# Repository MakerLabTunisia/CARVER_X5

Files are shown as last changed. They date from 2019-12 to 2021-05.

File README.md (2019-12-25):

# CARVER  X5, the Open source 5 Axis CNC Machine

# Story:

## MakerLab :

MakerLab is a Tunisian tech startup specialized in developing customized embedded systems and mechatronics projects to industrials.  
In MakerLab, we believe in the Open Source Hardware philosophy and we want to spread the tech knowledge we gain, with the community so everyone performs itself and benefits from others experiences.        And this is why, we made from our little space in Sousse, a **TechSpace**, open for everyone who wants to work on real projects, finding all what a Maker needs to create his own tech project.  
In our TechSpace, many projects were developed and created, even if it is by our staff or by students from different universities across the country, starting from Drones, Internet of Things (IoT) devices, arriving to Robotic Arms and CNC Machines.  
Moreover, this 5 Axis CNC Machine, is our first Open Source Hardware Project we made, and which we are so happy sharing it with the community. 
You can find more details on our TechSpace in our:  
Lien Facebook : https://www.facebook.com/tunmakerlab/
Lien siteweb : https://makerlab.tn/

## Presenting the project:

This 5 axis CNC machine, is part of a big project made by our partners Open Lab Hamburg from the Helmut Schmidt University in Germany, for the benefit and with the collaboration of FABLAB ENIT (National School of Engineering of Tunis), and sponsored by the BMBF. 

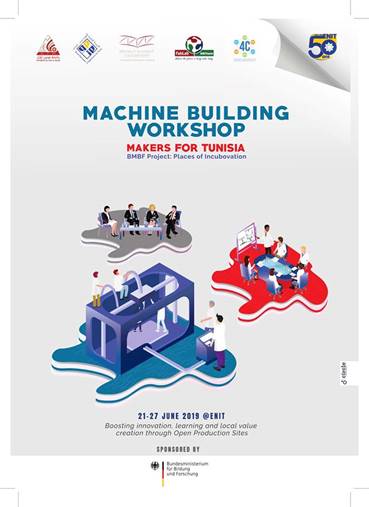
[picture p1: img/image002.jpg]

<div align="center"><i>Machine Building Workshop</i></div>
This project consists of organizing a one-week workshop for building machines, and we, MakerLab’s staff, are happy and glad to be part of this first of its kind project in our beloved country, Tunisia.

# Why a 5 axis CNC Machine?

Being always updated to the latest OSHW projects in the community, we found that there is many 3 Axis CNC machines, 3D Printers and Laser Cutter with a very good documentation, but not enough OSHW 5 Axis CNC machines and not at all for the Head/Head type. 

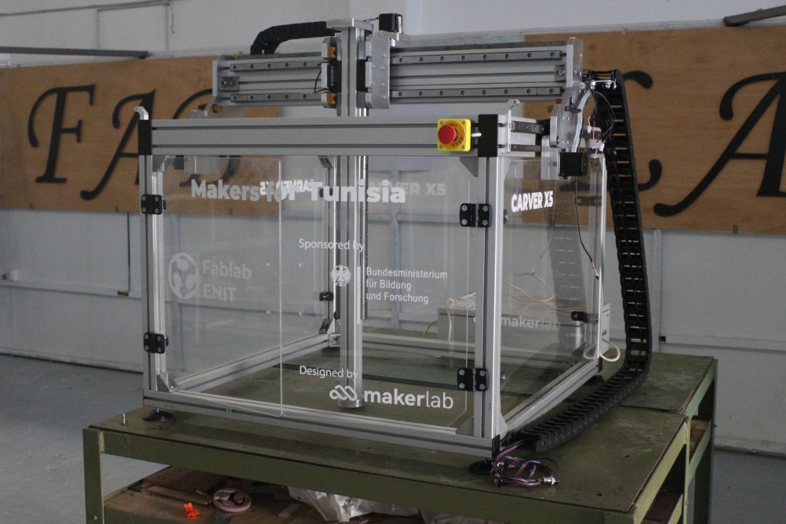
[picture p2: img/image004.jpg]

<div align="center"><i>CARVER X5 Machine</i></div>
So we thought we could create the first OSHW, Head/Head, double swivel head form, 5 Axis CNC Machine. We tried our best to make it both robust and easily replicable machine. Constructed mainly from Heavy Aluminum Extrusion profiles, and thick aluminum milled parts, HGR25 Linear guides, using NEMA23 Stepper motors, and Rack and pinion for transmission, Carver X5 is capable of milling materials like wood, plastics and composite materials.

# CARVER X5 Machine

## 1. Specifications

**Dimensions 5xm600** 	      : 650 x 670 x 480mm  
**Working volume 5xm600**   : 990 x 780 x 1000mm  
**Max travel speed XYZ**	      : 15000mm/min (X,Y);     3000-6000mm/min (Z)  
**Max travel speed BC**            : 20rpm(C)  20rpm(B)  
**Motors used**                           : NEMA 23 ( X / Y / Z / B / C)  
**Linear guides**                         : HIWIN High accuracy Rails and Blocks  
**Structure material**               : Anodized Aluminum   
**Protection**                              : 5mm Acrylic enclosure  
**Power requirements**           : 1200W, 220V, 60hz, 13A   
**Weight**        	           		      : 85kg  
**Computer interface**             : USB  
**Computer requirements**    : Windows operating system with Mach3  
**Controller**                               : MACH3 (to be purchased separately from an official vendor)  
**Software**                                 :  supports any CAD/CAM software   

## 2. Machine design

CNC machines are commonly known that they are nothing more than automated robots, their famous type, is a 3 axis CNC machines, which are considered as 3P robots (robot with 3 Prismatic Joints linked with 4 Links).  

But in 5 axis CNC machines we talk about 3P2R robots, because they are composed of 3 Prismatic Joints succeeded with 2 Revolute Joints, and linked with 6 Links.

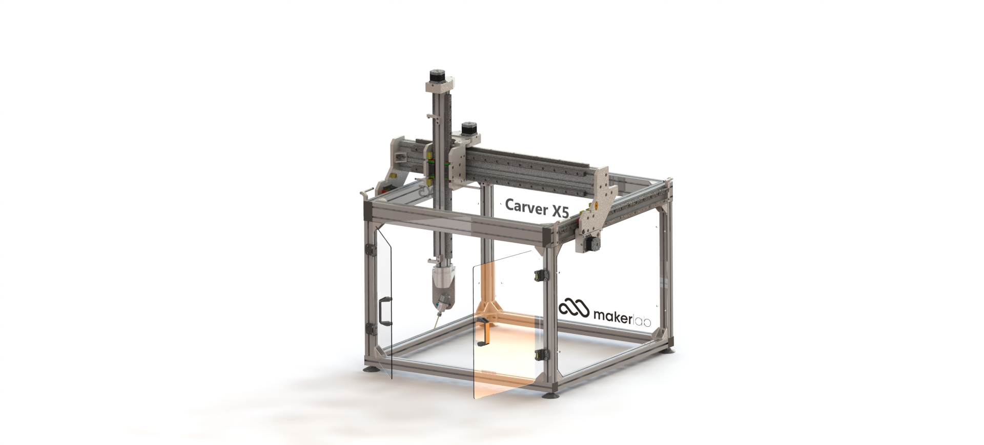
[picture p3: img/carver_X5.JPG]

<div align="center"><i>CARVER X5 Design</i></div>
Our Joints are named (X, Y, Z, C & B)

The Links are named : Frame, Y2X Bridge, X2Z, Z Axis, Swivel Head and the Spindle.

## 3. Machine composition:

### ▪ Frame 

Designed to be easily made, assembled and disassembled, we choose the aluminum profile to be the main structure composition.
As it's important that the structure be stiff and robust, we wanted to work with 45 series aluminum profiles.

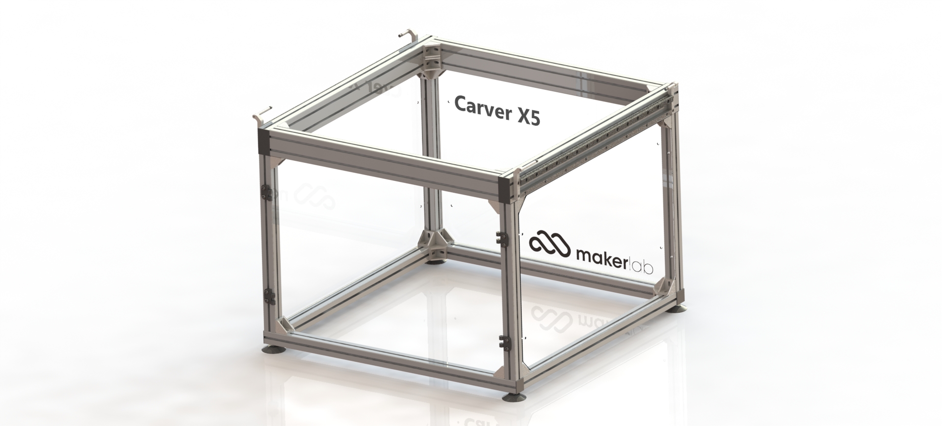
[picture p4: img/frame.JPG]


<div align="center"><i>Machine Frame</i></div>
The machine frame contains the rails and transmission rack of the Y-axis that will carry the other entire axis, this is why we worked with the 45x90 aluminum profiles in the top stage.
The frame carries the mechanical stops; they include a screw to adjust the limit position.

### ▪ Y2X Bridge

The Y2X Bridge is the second link in our 5-axis CNC machine, it links the Y and X joints.

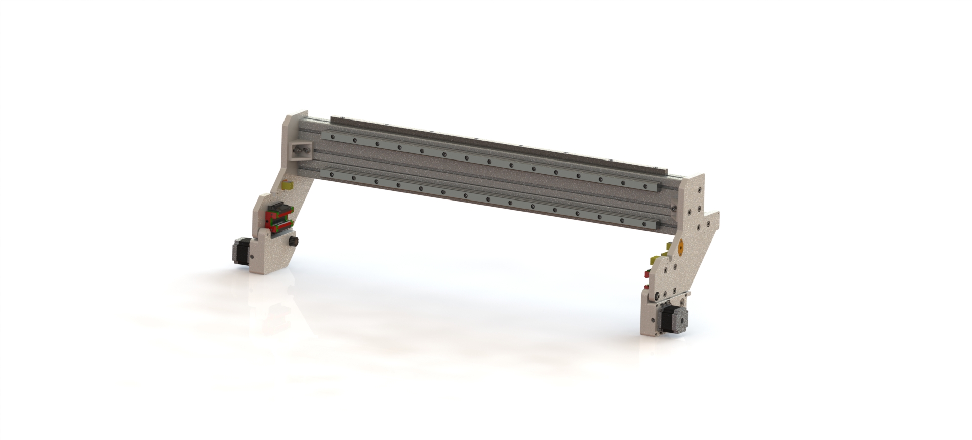
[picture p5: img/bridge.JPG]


<div align="center"><i>Y2X Bridge</i></div>
Constructed from two perpendicular 45x90 aluminum profile and two 15mm aluminum plate flanks on which will be installed the Y-axis sliding blocks.

### ▪ X2Z 

X2Z, as its name indicates, do the function of the joint between the two prismatic axis, X and Z.
X2Z is an assembly that plays a big role in our 5 Axis CNC Machine, because it assures both, the linear guiding of X axis, Z axis and their transmission organs.

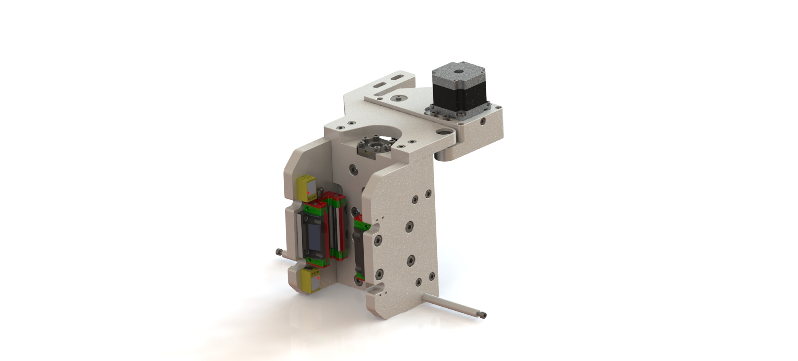
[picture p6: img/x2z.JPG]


<div align="center"><i>X2Z</i></div>
Built totally from thick aluminum plates, X2Z contains the sliding blocks of X-axis installed on its back, and those of the Z-axis, installed between the two X2Z flank plates.
On the X2Z assembly, get installed the X Motor Module and the Z-axis ball bearing Nut.

###  ▪ Z Axis

The Z-axis, slides on the 2 blocks installed on the X2Z Flank plates. The motor module installed on its top assures its motion. The Z motor transmit rotation to the ball screw that moves the Z-axis up and down.

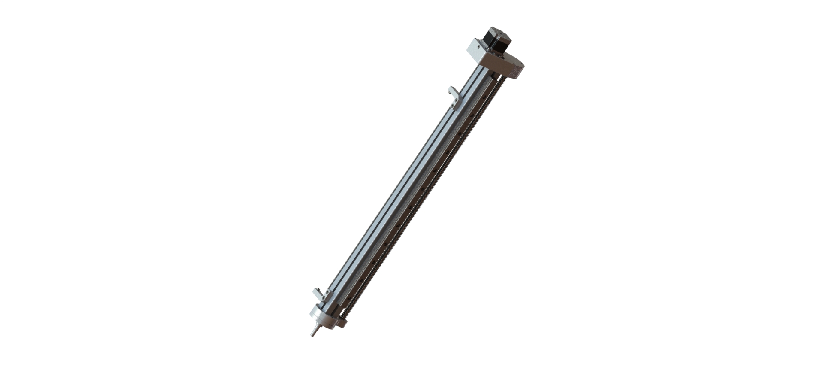
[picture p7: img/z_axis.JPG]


<div align="center"><i>Z Axis</i></div>
In its bottom is installed the swivel head that rotates the end effector around 2 axis.

###  ▪ Swivel Head

The swivel head is composed from the last two revolute joints, C & B.
What is special about this assembly, is the fact that it should be the more compact possible. So the two motors, their transmission system and even the limit switches and connectors should all be enclosed in this assembly, and this was the hardest task that we encountered in the whole machine design.
While designing the Swivel Head, there was 2 big challenges, the choice of transmission system and minimizing joints offset relatively to each other.

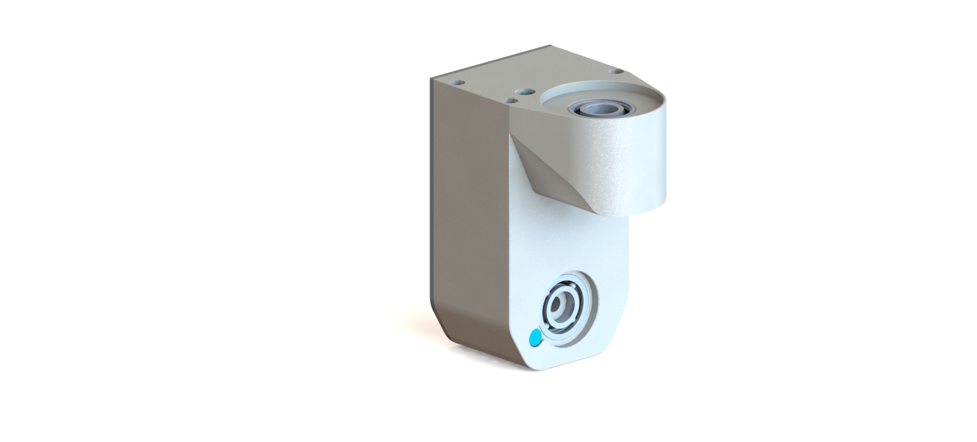
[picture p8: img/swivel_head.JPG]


<div align="center"><i>Swivel Head</i></div>
There is challenge because C and B axis will handle big effort while milling, and if mounted directly on the motor shaft or even through a reversible transmission system, this may cause a loss in steps when encountering big efforts. This obliged as to work with worm gear, which is an irreversible transmission system.

### ▪ Spindle Motor

For the spindle motor, we did our best to find small and powerful, and not too expensive ones in the market, but we found none.
The main specification needed is a small size, but the most of powerful spindles are so big that you cannot integrate in the swivel head.
This is why we designed and fabricated our own spindle composed of a 540W Brushless motor, a bearing housing and an ER11 chuck.

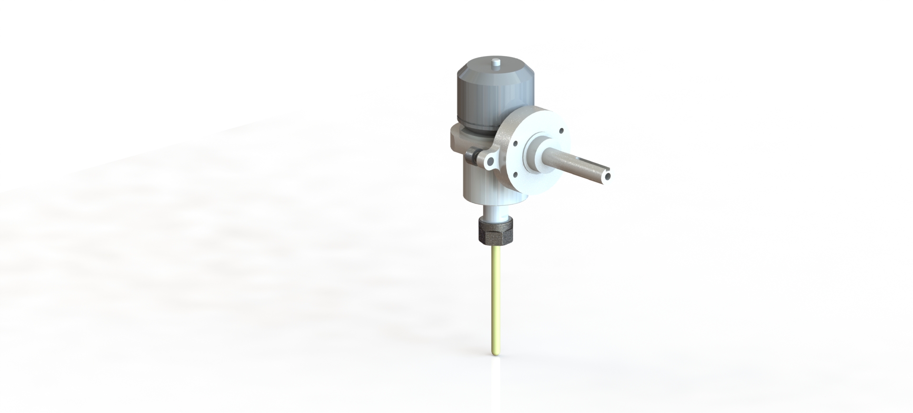
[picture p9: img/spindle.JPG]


<div align="center"><i>Spindle Motor</i></div>
The spindle motor is capable of a max velocity of 20000 RPM at 24V, and has enough torque for milling wood and plastics.

### ▪ Motor Modules

Machine movement along X, Y and Z Axis is assured by 4 motor modules.  Containing pulley and belt transmission system between the motor shaft and the shaft.

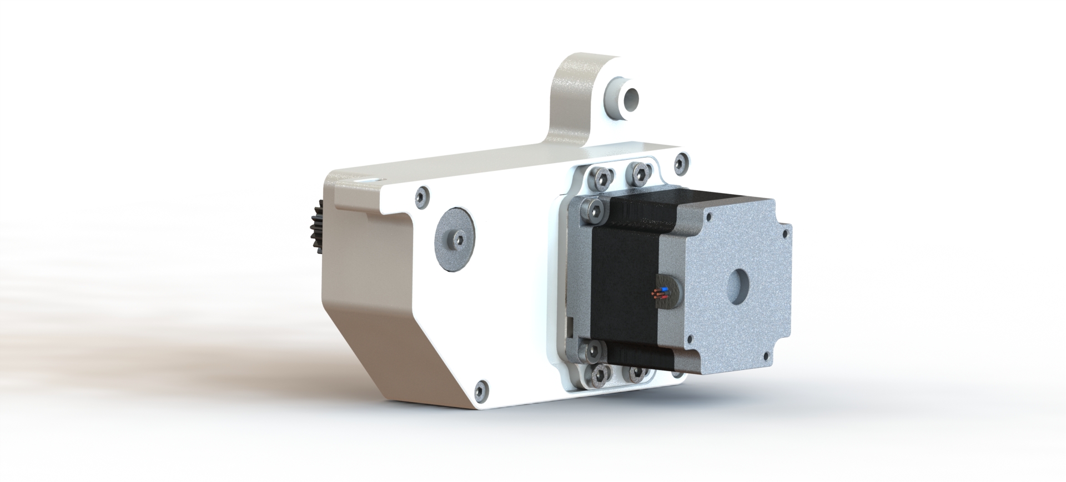
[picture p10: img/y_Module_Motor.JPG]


<div align="center"><i>X/Y Axis Motor Module</i></div>
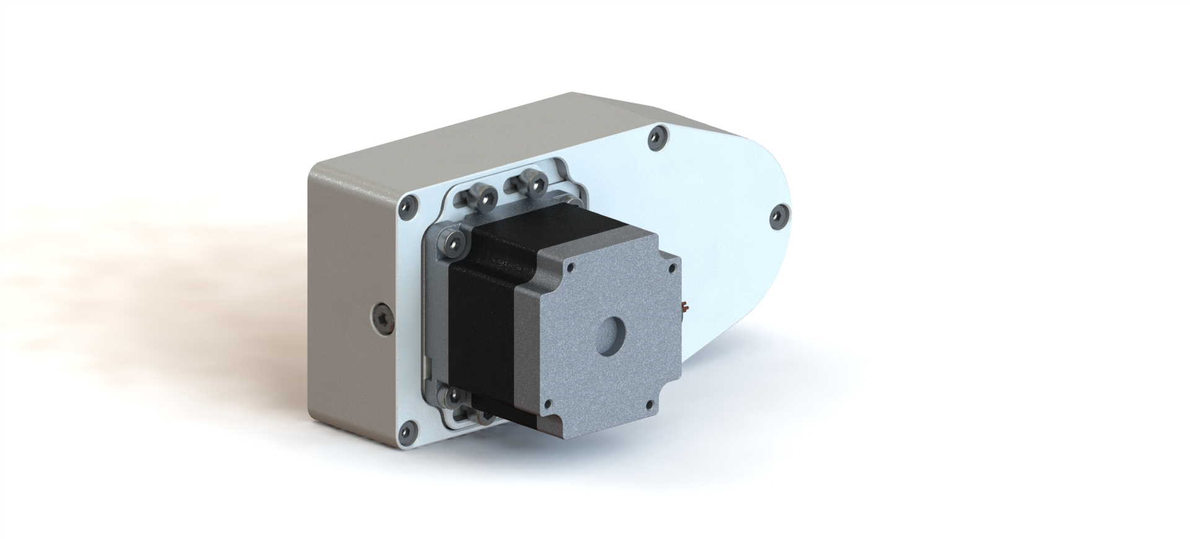
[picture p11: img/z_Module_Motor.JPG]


<div align="center"><i>Z Axis Motor Module</i></div>
## 4. Electronic enclosure

Installed in an industrial **[plastic enclosure](http://www.akisplastik.com.tr/en-us/Product/ProductCategoriesDetail?categoryId=12)** (400x500x240), the **electronics** of the **CARVER X5** is composed of a set of drivers for each motor including the spindle driver, a USB interface control board, a sensor interface board and two 12v 42A DC Power Supply. 

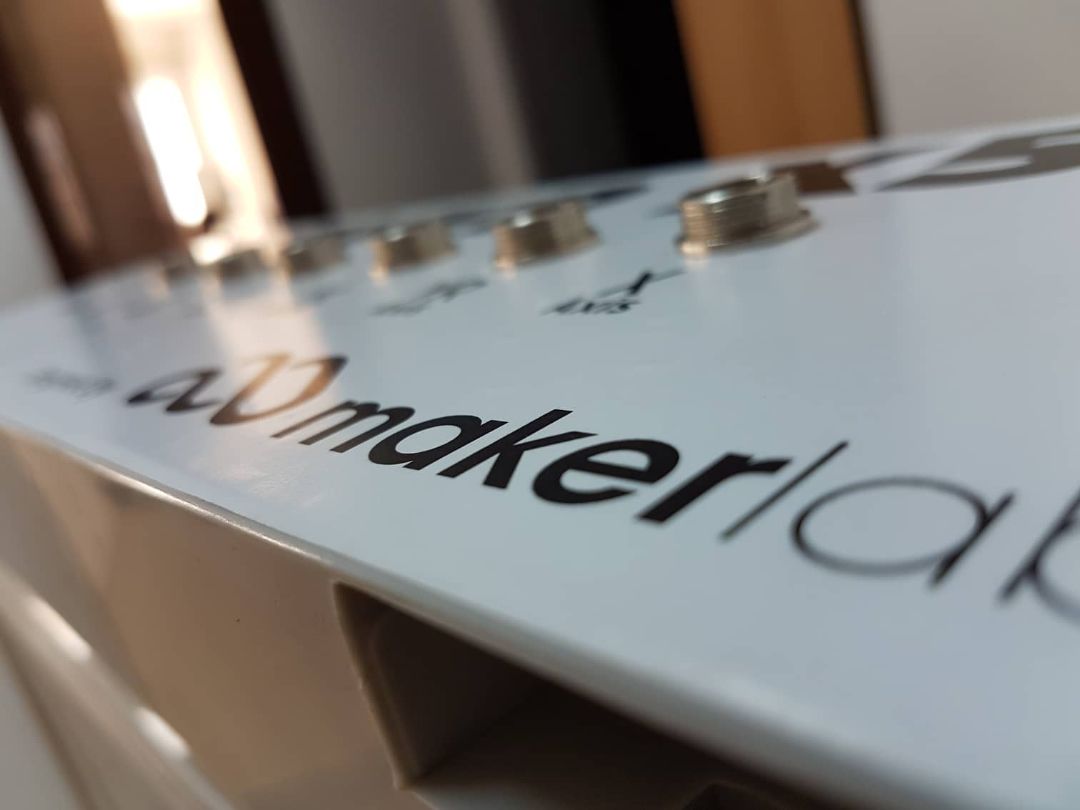
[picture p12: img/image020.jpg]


▪ **THE PoKeys57CNC control board**
PoKeys57CNC USB and Ethernet CNC controller is a blend between general purpose PoKeys device and motor controller. The device is targeted primarily for controlling up to 8 STEP/DIR signal driven motors (stepper motors, servo drives, etc.) in various applications with the addition of powerful PoKeys device features. 

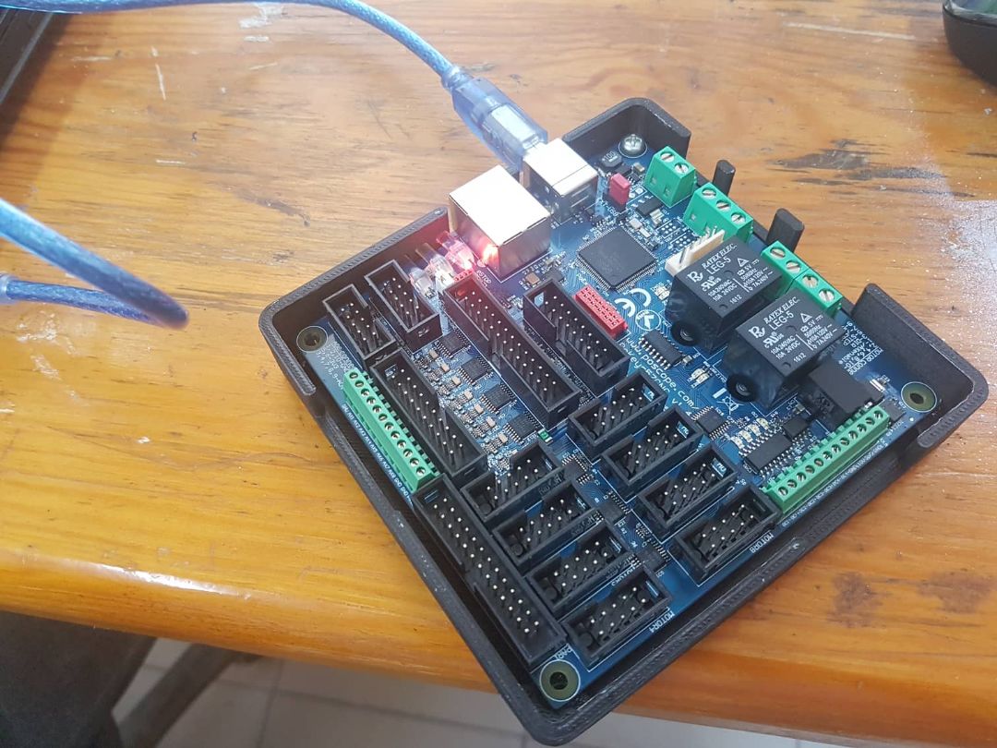
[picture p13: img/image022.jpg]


 Download PoKeys57CNC datasheet [here](https://www.poscope.com/wp-content/uploads/downloads/Pokeys/Manuals/PoKeys57CNC%20user%20manual.pdf).

▪ **Drivers**
TB6600 Stepper Motor Driver is an easy-to-use stepper motor driver, which could control a two-phase stepping motor. It is compatible with Arduino and other microcontrollers that can output a 5V digital pulse signal. TB6600 stepper motor driver has a wide range power input, 9~42VDC power supply. And it is able to output 4A peak current, which is enough for the most of stepper motors. The stepper driver supports speed and direction control. You can set its micro step and output current with 6 DIP switch.

Download TB6600 datasheet [here](http://olimex.cl/website_MCI/static/documents/TB6600_data_sheet.pdf).

▪ **The sensor cables gatherer board**
The need for the sensor cable gatherer board has emerged due to the multiplicity of sensors. And to minimize the number of cables passing through the cables carrier, first, we managed to gather them in a 15 cores VGA cable, then we choose to use 2 DB9 ports and cables, one for Limites (+), and the other for Limites (-).  

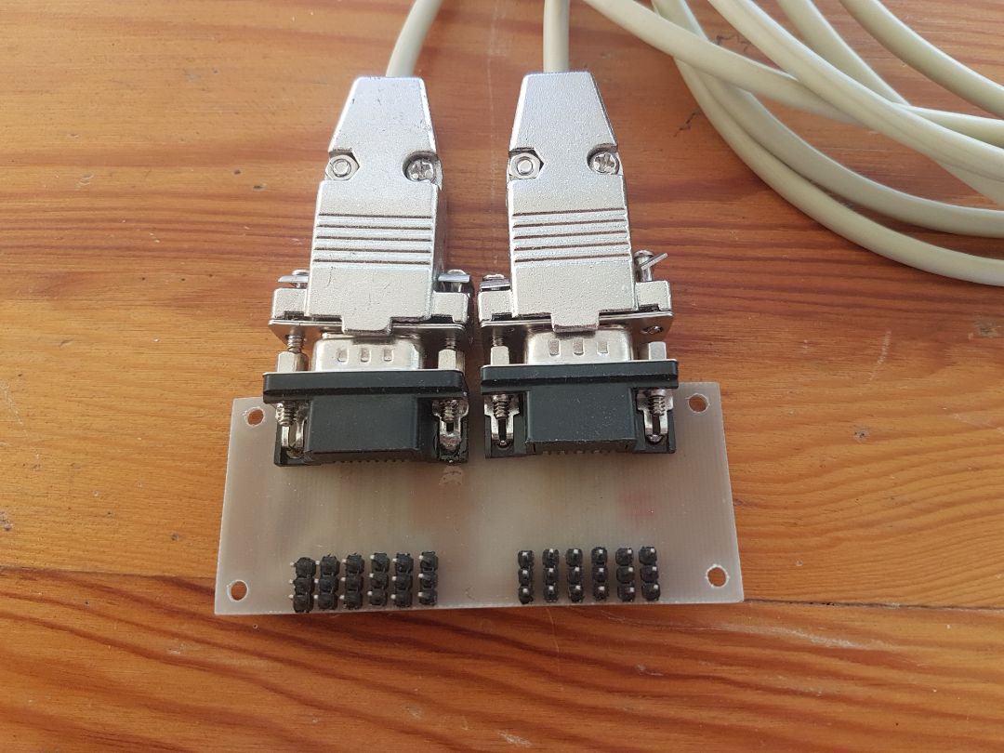
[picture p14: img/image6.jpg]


This board provides the current and voltage needed to all the 10 sensors used in the machine and the toggle switch, and is installed on the Y2X Bridge in between the two cables carrier.   

(Board KiCAD)

▪ **The sensors interface board**
This board will play the role of the interface between sensors signals coming from the first board and the pokeys57cnc board through a little circuit of signal adaptation.  
Inductive proximity switches works with 12V power supply, and returns a 12V digital signal, but the pokeys57cnc can only handle 5V digital signal in limit switches inputs. 

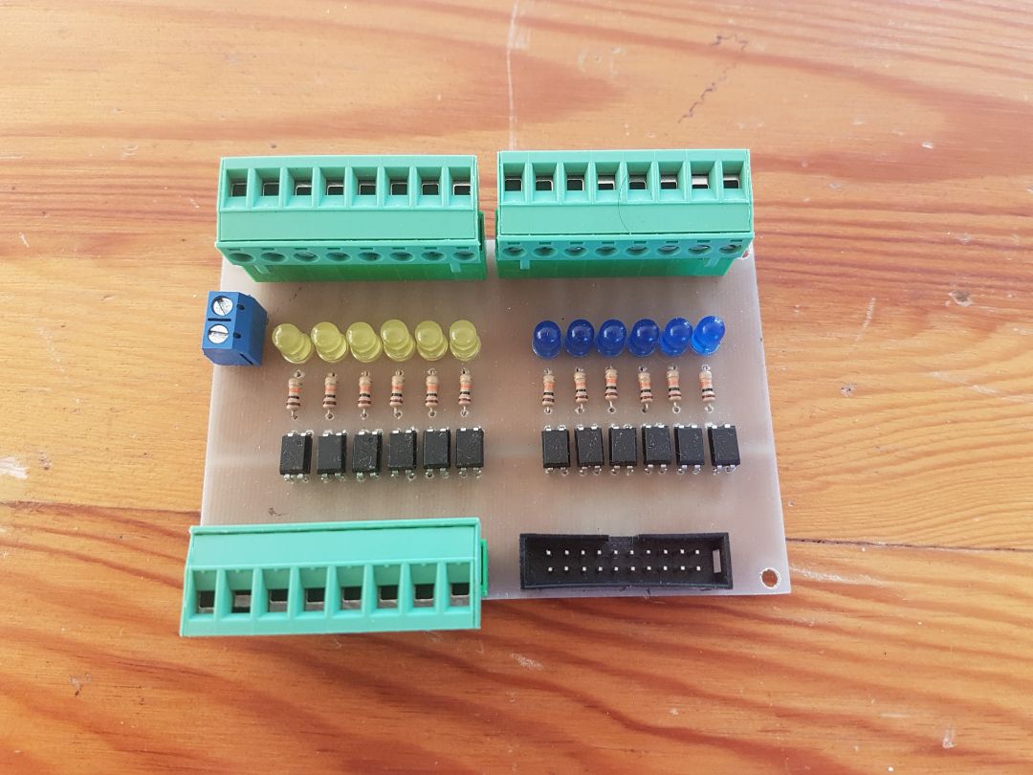
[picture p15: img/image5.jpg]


This is why we used a circuit based on a 470 ohm resistor for current limiting and a 5.1V zener diode to let only the needed 5V pass to the control board for each signal. 

▪ **Spindle motor Driver**
As we created our own spindle based on brushless DC Motor, we used its recommended Electronic Speed Controller as a driver. A 60A ESC is responsible of driving the motor at 20 000 RPM at 24V.
Product page [Link](https://www.overlander.co.uk/overlander-xp2-60a-sbec-brushless-esc-rtf-speed-controller.html).

## 5. Wiring

 One main task we did is the wiring, and it is so important.
 We used RGB 4 wire Cables for the stepper motors, they are thick enough to carry the needed current.
 The end stop switches cables were long enough to reach the first interface board installed on the bridge assembly.
 We gathered all sensors signals in two RS232 cables to facilitate connection.
 Of course all these cables needed a way to be placed in, so we used 57x25 industrial cable carrier to arrange all wires to the electronic enclosure.

## 6. Software

### ▪ Fusion360 : CAM software
Fusion 360 combines industrial and mechanical design, simulation, collaboration, and machining in an integrated concept-to-production toolset.
Fusion 360 is the first 3D CAD, CAM, and CAE tool of its kind. It connects your entire product development process in a single cloud-based platform that work both on PC and MAC.

Download [Link](https://www.autodesk.com/products/fusion-360/students-teachers-educators).

### ▪ Pokeys Software : Software for the CNC Interface Board
PoKeys software setup package contains PoKeys configuration tool (also used for firmware updating), USB drivers, manuals, PoBlocks tool, Mach3 plugin etc. After installation, run the PoKeys application to update the firmware of PoKeys devices.

Configuration explanation video [Link](https://www.youtube.com/watch?v=qxPZVYqWExU).

Download [Link](https://www.poscope.com/downloads/).

### ▪ Mach3 : CNC Machine Controller Software

Mach3 turns a typical computer into a CNC machine controller. It is very rich in features and provides a great value to those needing a CNC control package.

Configuration explanation video [Link](https://www.youtube.com/watch?v=e5MjEEe-gE4&t=58s).

Download [Link](https://www.machsupport.com/downloads-updates/).

# Machine Building Workshop

The Machine Building Workshop was a great experience to all of us, and it was the first step to sharing knowledge with everybody.

This is a set of photos describing the general atmosphere in which passed this wonderful workshop.

## **▪ Day 1** 
**Ice breaking & debriefing around CNC machines and their purposes**
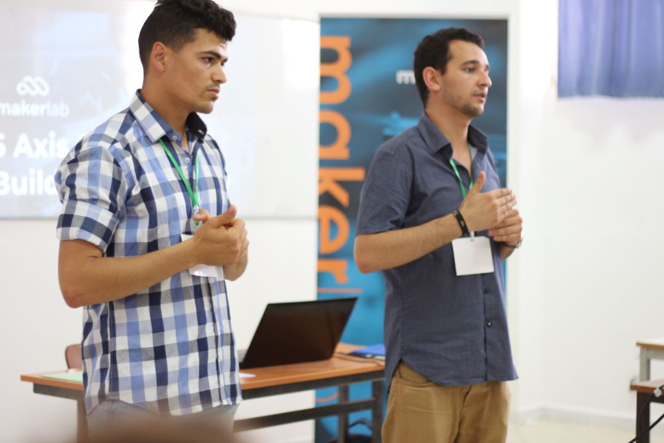
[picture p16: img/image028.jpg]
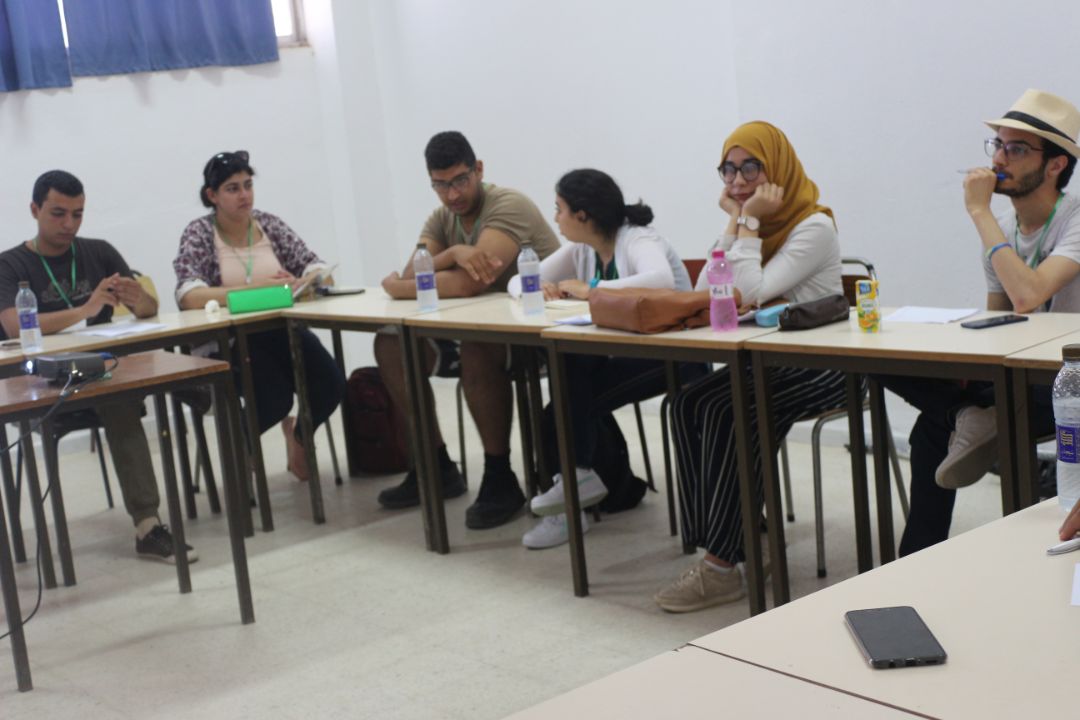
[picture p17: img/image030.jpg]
 

## ▪ Day 2 
Knowing everything about the design of the **CARVER X5** and the different steps will do during the workshop

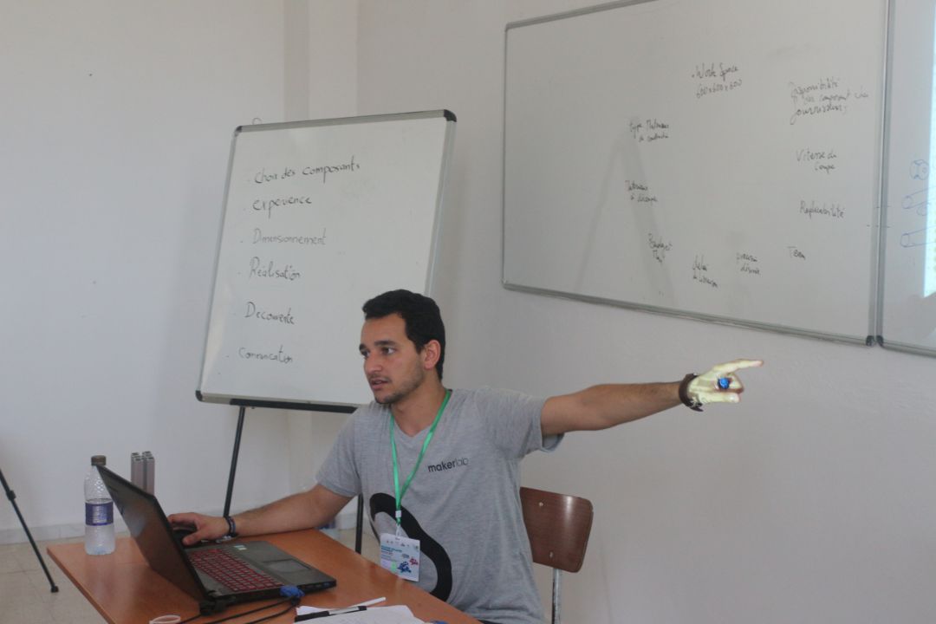
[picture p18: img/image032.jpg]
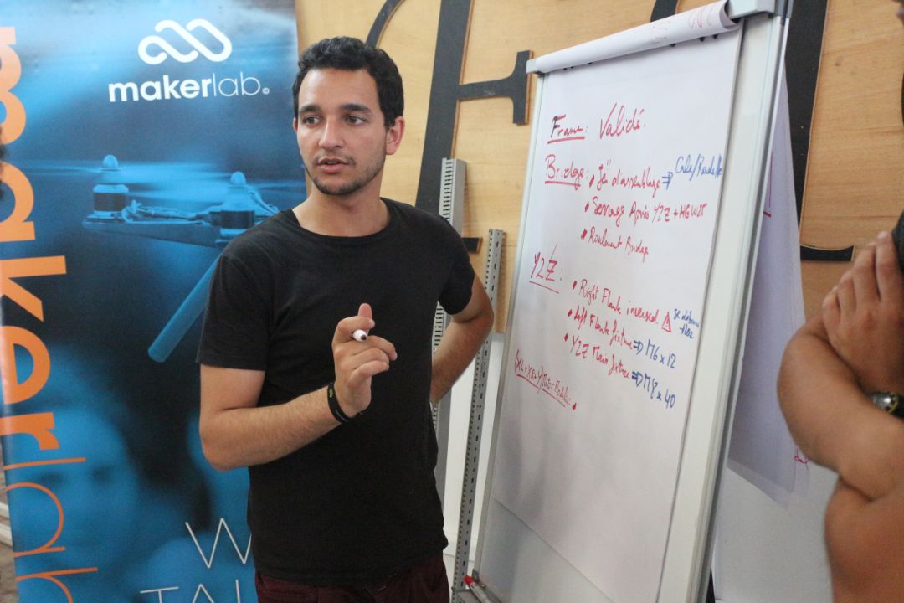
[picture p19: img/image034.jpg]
 

## ▪ Day 3 

**-Workbench and space preparation** 

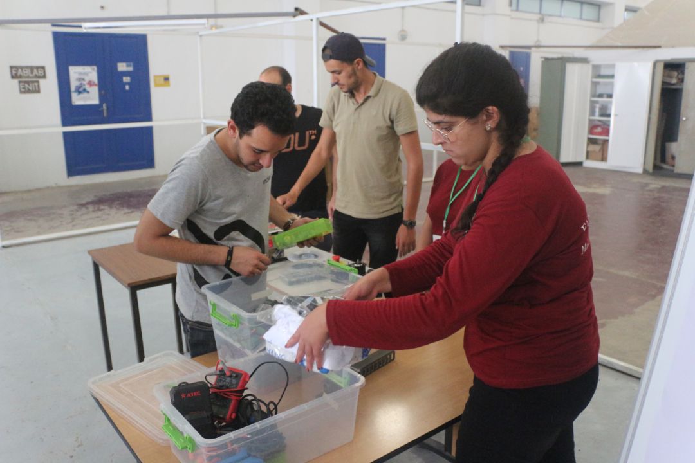
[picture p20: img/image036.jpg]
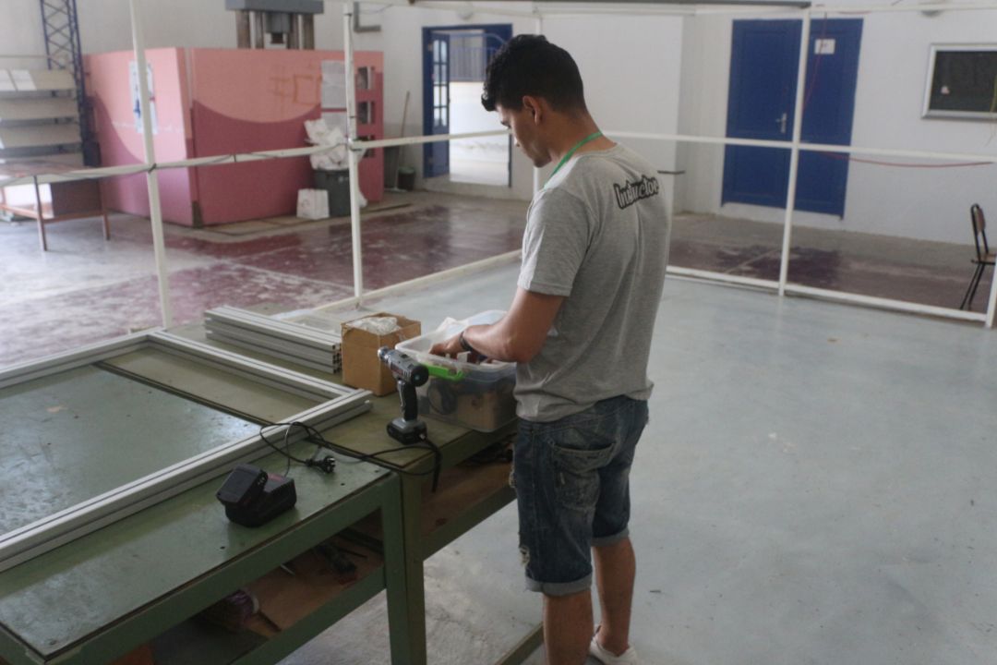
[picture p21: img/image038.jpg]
 

**-Frame assembly**

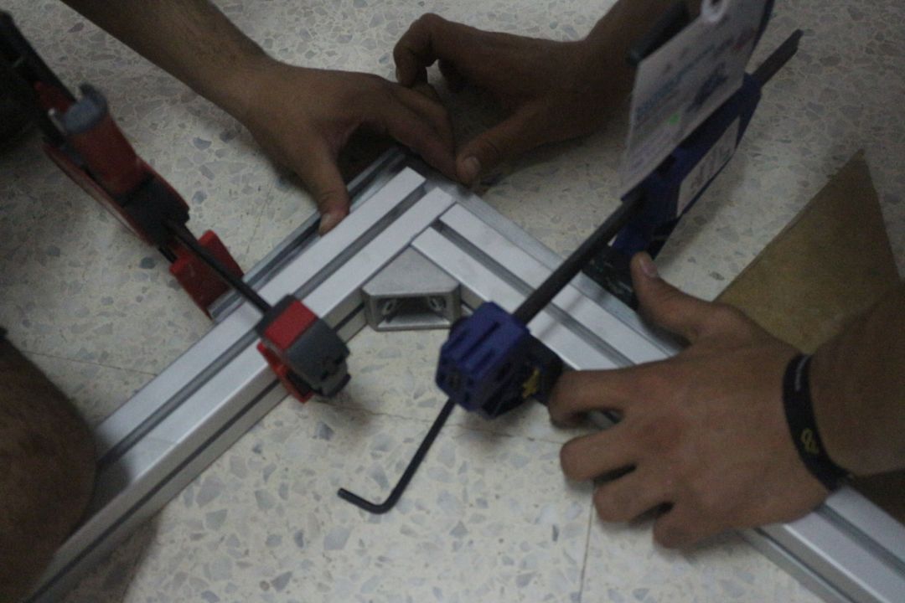
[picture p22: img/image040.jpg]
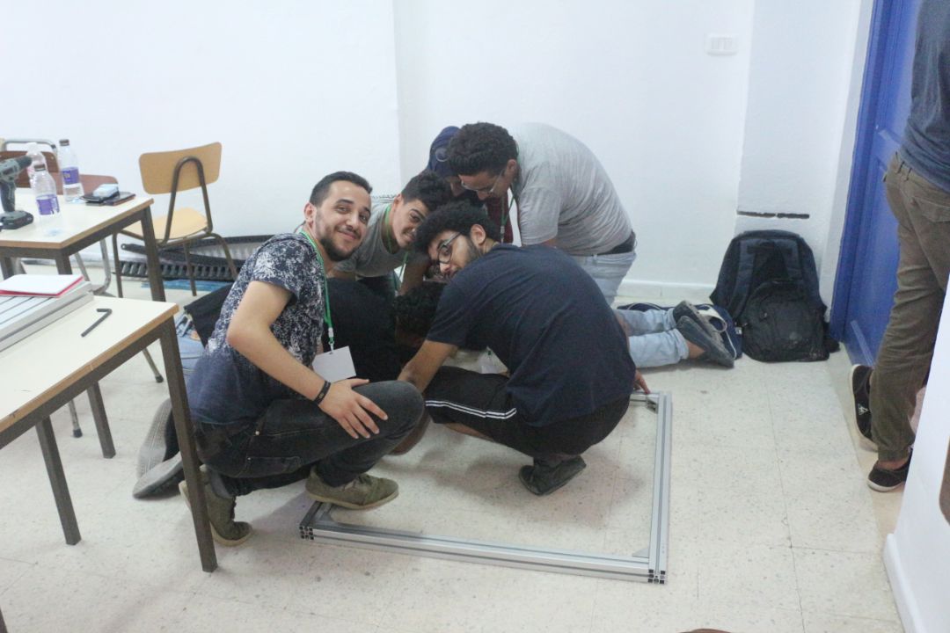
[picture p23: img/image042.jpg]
 

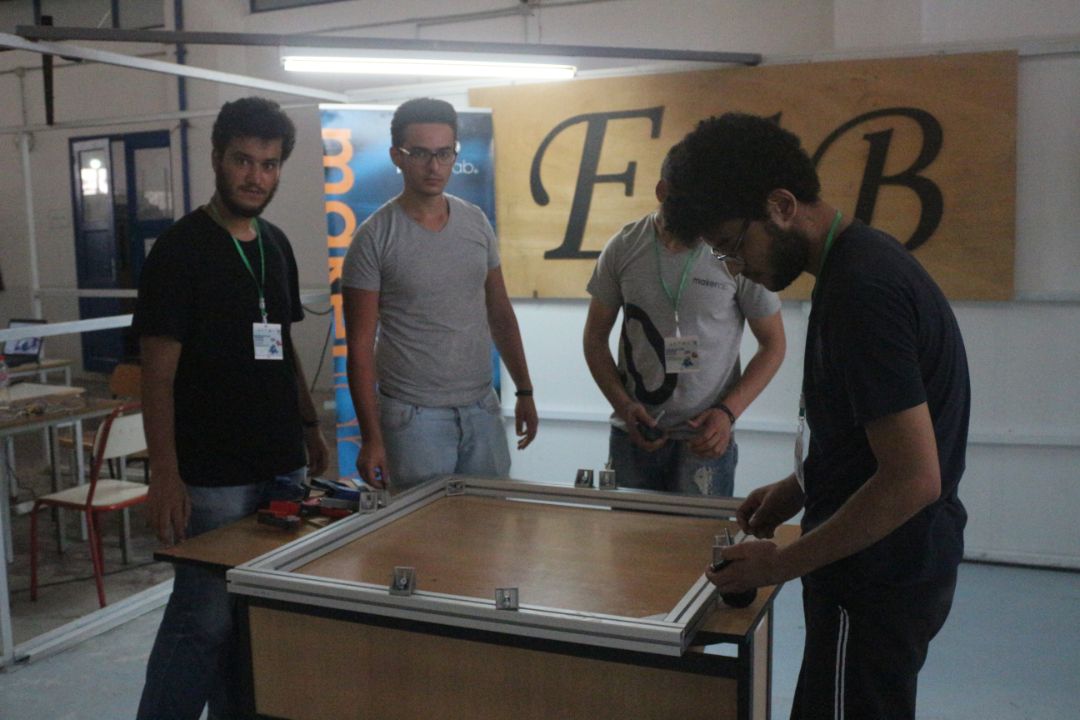
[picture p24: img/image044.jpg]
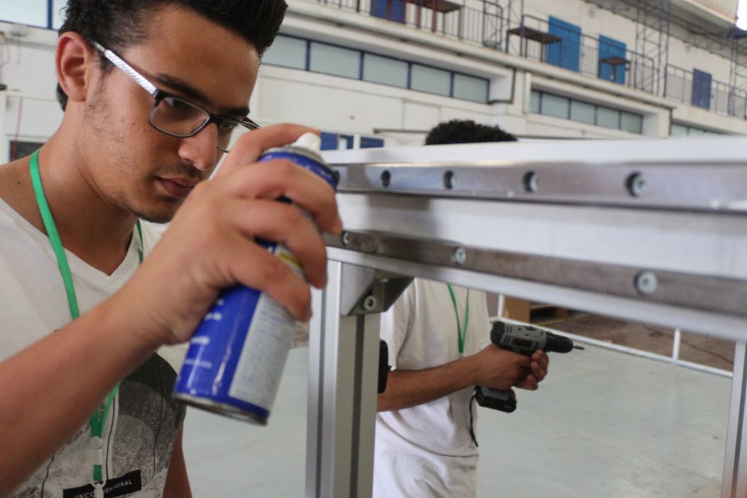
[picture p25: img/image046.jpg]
  

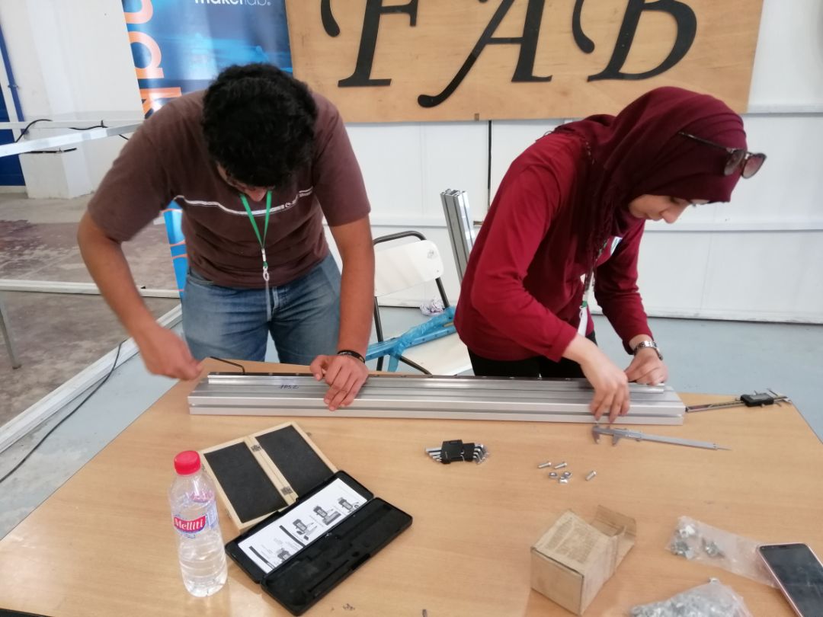
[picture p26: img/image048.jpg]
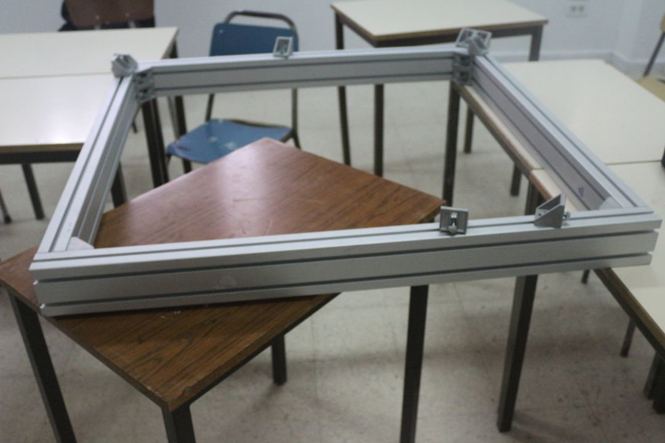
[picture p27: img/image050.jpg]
   

**-Electronic circuit schematic design**

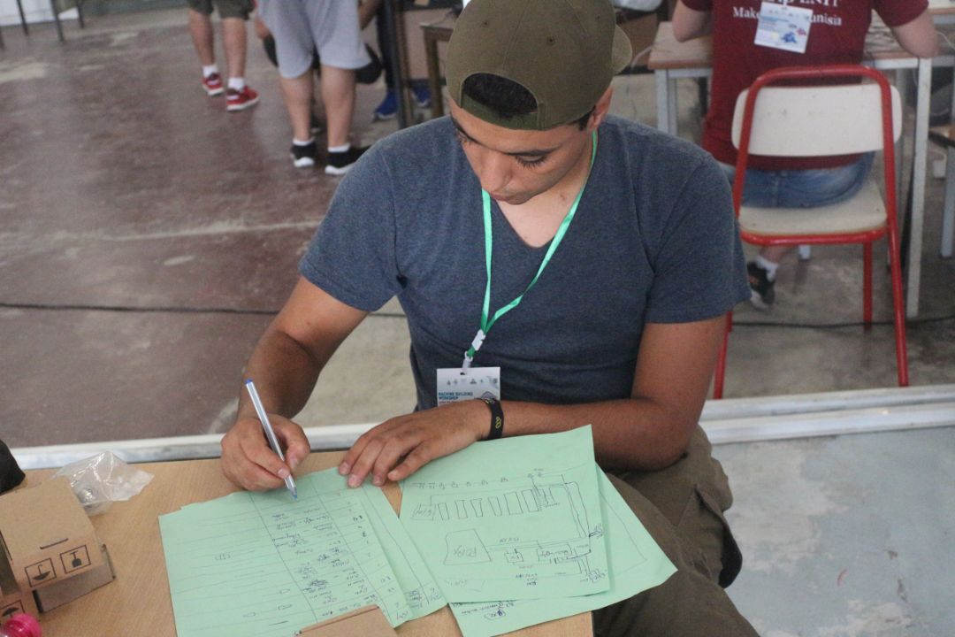
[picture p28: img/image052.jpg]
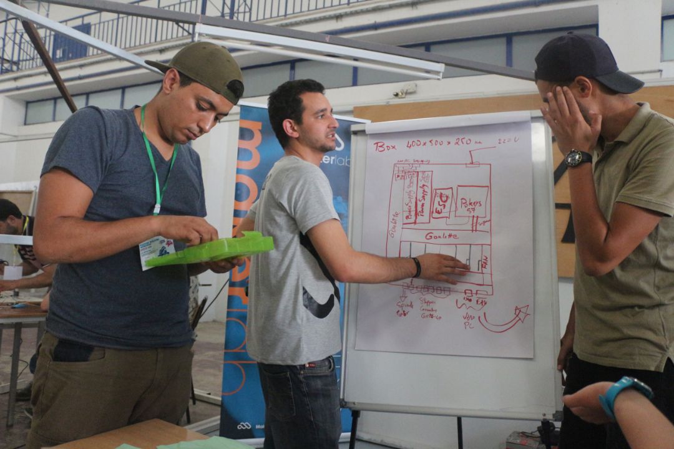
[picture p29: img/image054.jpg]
 

## **▪ Day 4 & 5**
**-Y2X Bridge Assembling**

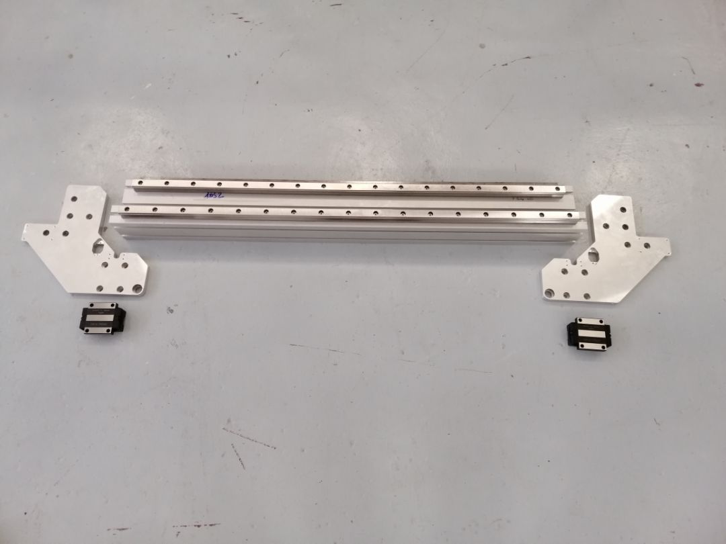
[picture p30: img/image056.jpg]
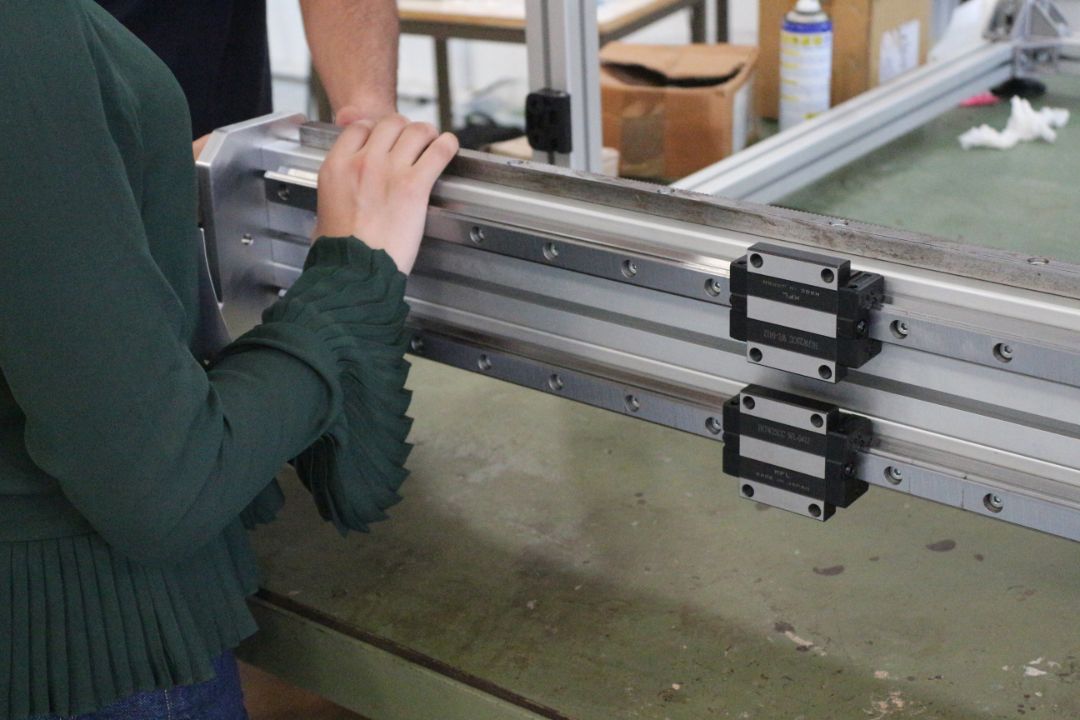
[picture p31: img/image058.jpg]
  

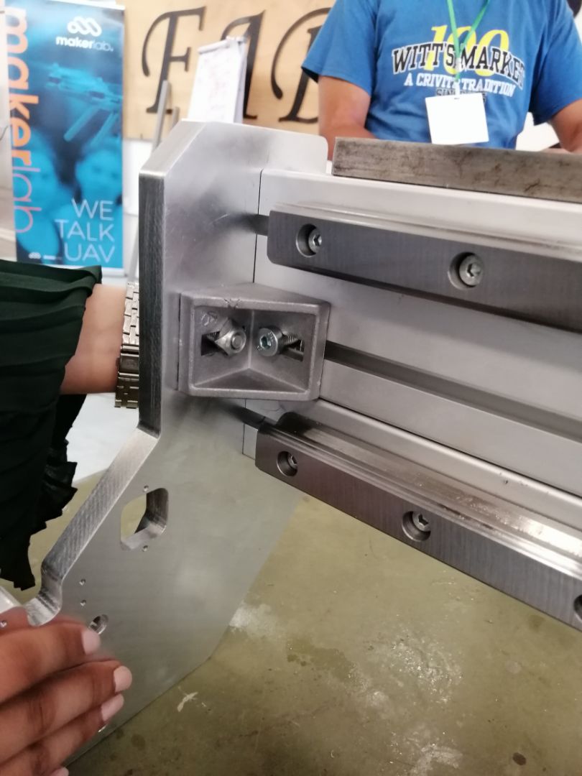
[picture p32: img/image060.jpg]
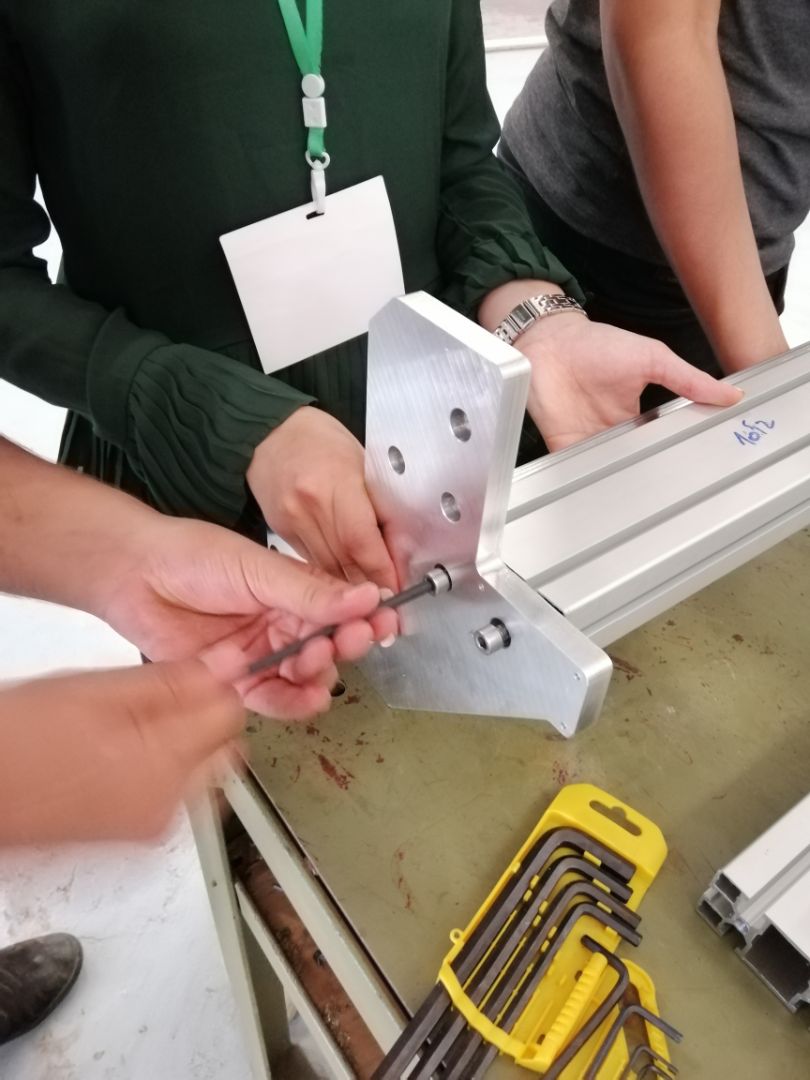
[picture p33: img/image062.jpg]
 

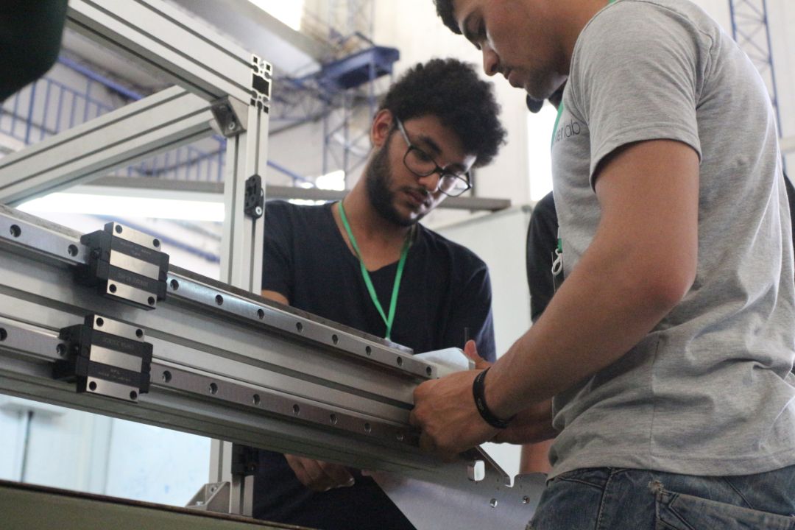
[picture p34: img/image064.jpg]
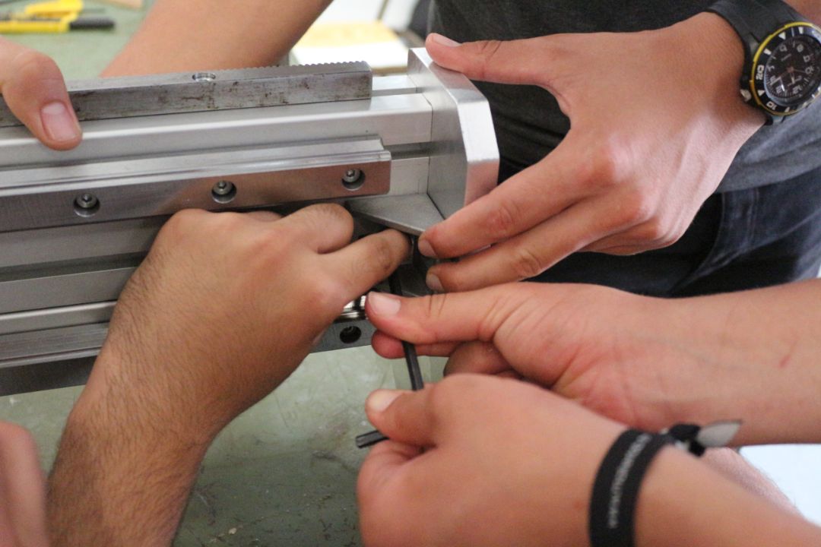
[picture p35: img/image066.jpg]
 

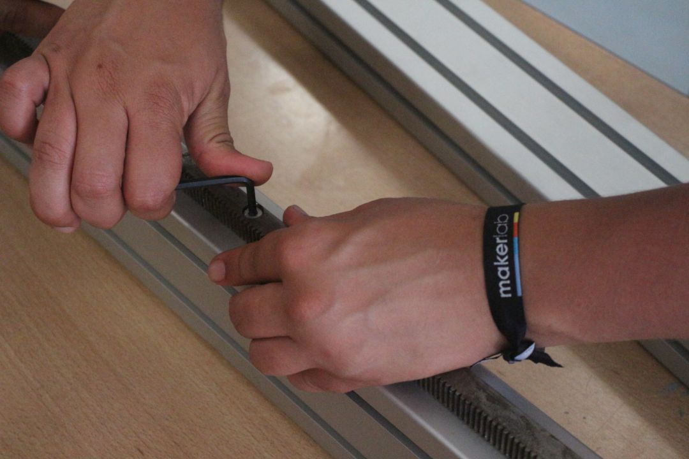
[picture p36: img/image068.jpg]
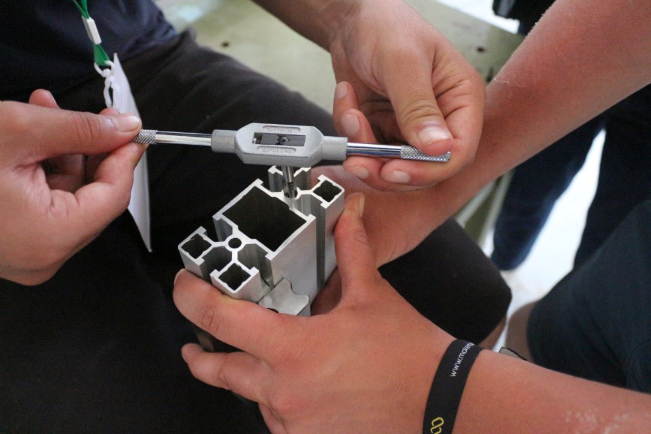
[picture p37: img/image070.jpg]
 

**-X2Z Assembling**

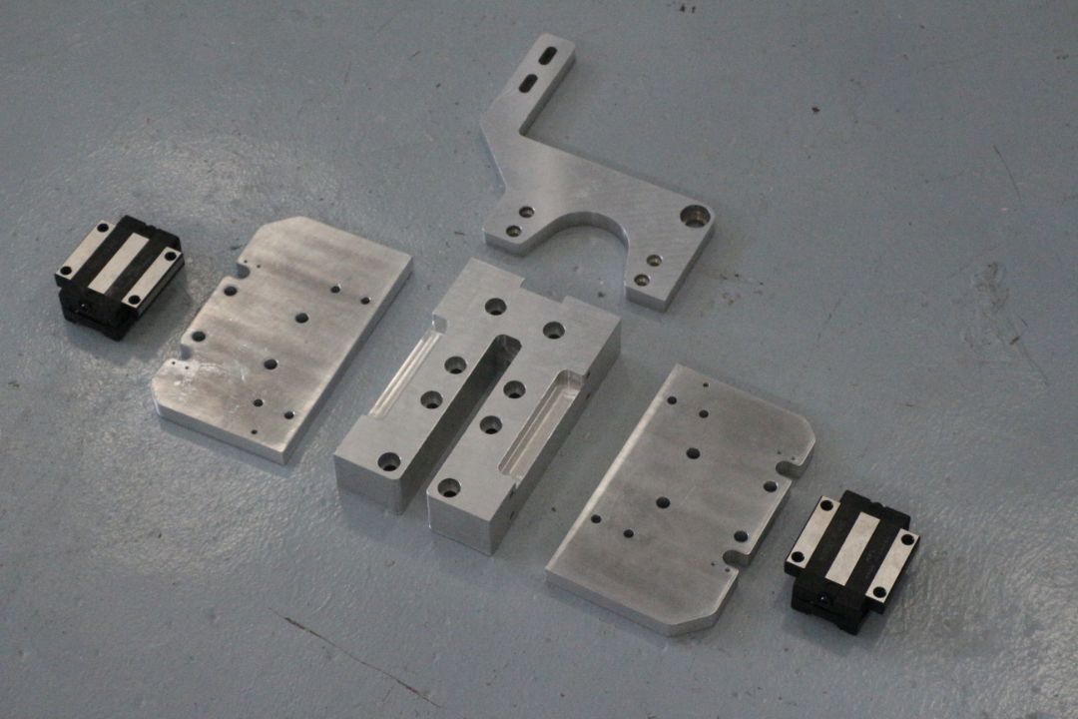
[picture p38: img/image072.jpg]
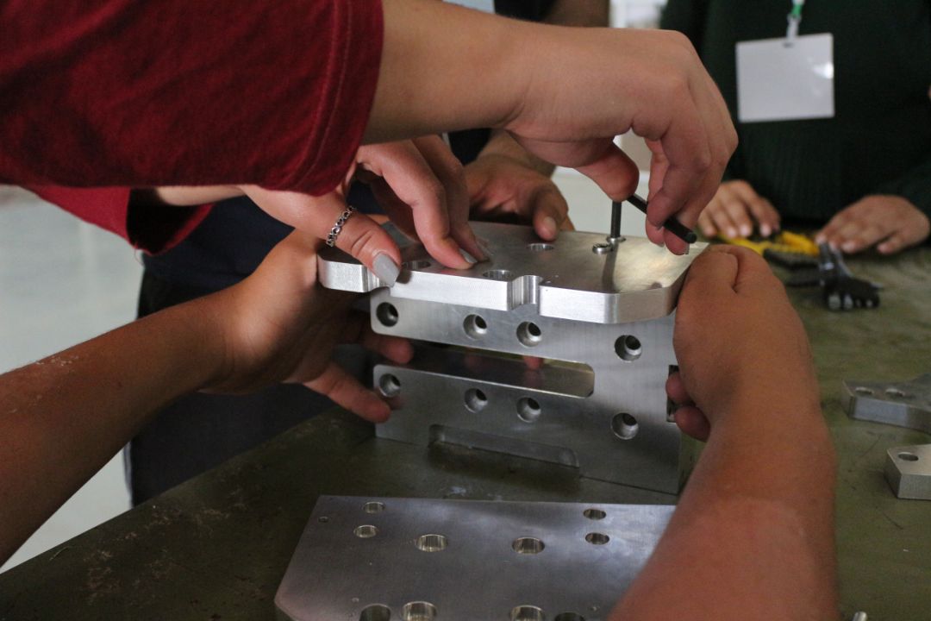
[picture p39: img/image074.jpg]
 

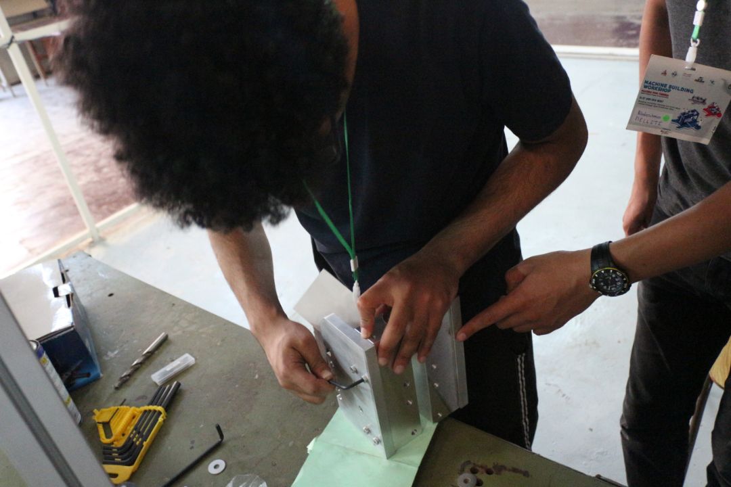
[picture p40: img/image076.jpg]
 

**-Electronic enclosure Assembling**

 

 

## ▪ Day 6 
**-Plexiglas enclosure assembling** 

 

 

**-Wiring electronic parts**

 

## ▪ Day 7 
**-Presenting the machine and Workshop roll up**

 

 

# Project progress

The project is still in progress, we finished the design of the whole machine, and the fabrication of the 3 first axis and all the electronic parts. Actually, we are manufacturing the double swivel head and the spindle system.
We moved the X,Y,& Z Axis with the Pokeys57 and Mach3, and we are working on the CARVER X5 post processor for FUSION 360.
We will update regularly this project in every progress we make, and we hope that this will be helpful for the whole OpenSourceHardWare Community !!
Don't forget to interact with us, send your notes or eventually you amelioration ideas !! 

# Credits

Everything has to end, and so did the **Open Source 5 Axis CNC Building Workshop**!
This workshop passed in an amazing way, and was a great success for all of MakerLab's team!
The knowledge of one month of machine design, followed by two months of fabrication and assembly, shared with amazing people from all over Tunisia, gathered in FabLab ENIT seeking one unique goal: Learn how to construct Machines! And today, this same knowledge is being shared with the whole DIY & Open Source Hardware community.

## Partners in the Workshop
This project was launched by Open Lab Hamburg from Helmut Schmidt University, sponsored by BMBF, which we thank a lot for their confidence and the opportunity they gave to us as a startup.
This Workshop was hosted by **[FabLab ENIT](https://www.facebook.com/FabLabENIT/)**, and was successful thanks to the devotion of the participants who are from now on **"Machines Makers"**.

## Amazing people around us
We would like to thank all the **FabLab ENIT Team**, **4C Center**, **ENIT administrative staff** for their collaboration. 
Coaches **Danielli Ingressia**,  **Hashim Al SAKKAF** and **Kais ALILA**, three great Makers from the Open Source community that we had the opportunity to work and exchange ideas with.
All the gratitude and thanks to **Babasile Daniel**, for his support and encouragement. 
Special thanks too to our families and friends who supported us in this big challenge (Marouen FAKHFAKH and Rabie TAHRI)

## Makers who worked on this machine
**CARVER X5 Designers**
     -Anis TRIGUI - Project Manager, Machine Designer and Coach - CEO of MakerLab
     -Mohamed MAATOUG - Designer and Pedagogic Certified Coach - MakerLab member
**Makers of MakerLab**
Azer KHALED, Alaa MEJRI, Khalil SLAMA, Salem MBAREK, Amine MAHDHI, Jawher MANSOUR, Moez KAZDAGHLI, Yassine CHEOUR
**Machine Building Workshop Participants ( Green Team)**
Sinda BESROUR, Eya CHROUDI, Sahar FRIKHA, Mootaz BEN ZINOUBA, Hassen ARBI, Haythem LTIFI, Abderrahmen MELLITI, Youssef SAFER, Seifallah BOUCHOUCHA, Taha ISSAOUI.

## Technical Partners
And finally, we would like to thank our partners, without their help, we couldn't reach this milestone:  
- **[Fabrica-Numeric](https://www.facebook.com/Fabrica.numeric/)**
- **[ElFabSpace](https://www.facebook.com/elfabspace/)**
- **[Electronic Shop](http://electronic-shop.biz/)**

Stay tuned to learn about our new coming Open Source Machine that we are planning to construct.

# Contact

- **contact@makerlab.tn**
- **[Linkedin](https://www.linkedin.com/in/kais-alila-3a1b35163/)**
- **[Facebook](https://www.facebook.com/tunmakerlab/)**
- **[WebSite](https://www.makerlab.tn)**

# Acknowledgements

The development of this machine has been funded by:<br>
**[German Federal Ministry of Education and Research](https://www.bmbf.de/en/index.html)**

Funds implemented by:<br>
**[OpenLab Hamburg](http://openlab-hamburg.de/startpage/)**<br>
[Helmut-Schmidt-Universität Universität der Bundeswehr](https://www.hsu-hh.de/en/)<br>
Laboratorium Fertigungstechnik<br>
Holstenhofweg 85<br>
22043 Hamburg<br>

# License

<br />Ce(tte) œuvre est mise à disposition selon les termes de la <a rel="license" href="http://creativecommons.org/licenses/by/4.0/">Licence Creative Commons Attribution 4.0 International</a>.

# Note
This documentation will be continuously improved as soon there are updates and/or improvements on the machine.

# CARVER_X5
# CARVER_X5

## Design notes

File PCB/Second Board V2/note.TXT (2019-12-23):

- emprint conecteurs 
- ecarter l'espace entre les pistes et plan de masse

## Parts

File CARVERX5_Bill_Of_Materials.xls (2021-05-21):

NUMERO DE PIECE | No. ARTICLE | DESCRIPTION | QTE
Frame X Bot | 1 |  | 2
Frame Y Bot | 2 |  | 2
Alu Profile End Cap 45x45 | 3 |  | 4
nervure | 4 |  | 30
Articulated Foot | 5 |  | 4
Frame Z | 6 |  | 4
Frame X Top | 7 |  | 2
Frame Y Top | 8 |  | 2
Alu Profile End Cap 45x90 | 9 |  | 4
HGR25-R1000 | 10 |  | 4
Rack | 11 |  | 3
Y Axis Stop | 12 |  | 4
B18.3.1M - 6 x 1.0 x 16 Hex SHCS -- 16NHX | 13 |  | 64
B18.3.1M - 6 x 1.0 x 20 Hex SHCS -- 20NHX | 14 |  | 72
EndStop Spacer 75mm | 15 |  | 2
EndStop Spacer 40mm | 16 |  | 2
Back Plexi Panel | 17 |  | 1
Lateral Plexi Panel | 18 |  | 2
Charnière Polyamide | 19 |  | 8
B18.3.1M - 8 x 1.25 x 16 Hex SHCS -- 16NHX | 20 |  | 34
Bridge Aluminium Extrusion | 21 |  | 2
Bridge Right Flank | 22 |  | 1
Bridge Left Flank | 23 |  | 1
HGW25CC | 24 |  | 6
Inductive Switch Holder | 25 |  | 2
TL-Q5MC1 Omron Proximity Switch Inductive Sensor | 26 |  | 6
B18.3.1M - 8 x 1.25 x 30 Hex SHCS -- 30NHX | 27 |  | 4
Bearing 608 | 28 |  | 3
Tendeur Moteur | 29 |  | 4
57BYGH201 | 30 | description | 4
Motor Pulley 17XL037 6.35mm Bore | 31 |  | 4
Gear Z20 m1 | 32 |  | 3
Motor Module Pivot Spacer | 33 |  | 3
Motor Module Pulley 17XL037 | 34 |  | 3
Motor Module Washer | 35 |  | 5
Rondelle Axe Module Moteur | 36 |  | 3
16002 | 37 |  | 6
Axe Module Moteur | 38 |  | 3
Wedge 3x3x14 | 39 |  | 6
DIN 6912 - M4 x 25 --- 14N | 40 |  | 17
DIN 6912 - M5 x 12 --- 7.8N | 41 |  | 27
DIN 6912 - M4 x 10 --- 6.5N | 42 |  | 10
DIN 6912 - M5 x 10 --- 5.8N | 43 |  | 12
YL Motor Module Gear | 44 |  | 1
YL Motor Module Motor Holder | 45 |  | 1
YR Motor Module Motor Holder | 46 |  | 1
YR Motor Module Gear | 47 |  | 1
Spring | 48 |  | 3
B18.3.1M - 5 x 0.8 x 40 Hex SHCS -- 22NHX | 49 |  | 3
B18.3.1M - 3 x 0.5 x 10 Hex SHCS -- 10NHX | 50 |  | 2
B18.3.1M - 3 x 0.5 x 5 Hex SHCS -- 5NHX | 51 |  | 2
B18.3.1M - 3 x 0.5 x 20 Hex SHCS -- 20NHX | 52 |  | 4
B18.3.5M - 3 x 0.5 x 8 Socket FCHS -- 8N | 53 |  | 4
AM-M8-N | 54 |  | 14
X2Z Main | 55 |  | 1
X Motor Module Support | 56 |  | 1
X2Z Left Flank | 57 |  | 1
X2Z Right Flank | 58 |  | 1
SFU1605 | 59 |  | 1
B18.3.1M - 3 x 0.5 x 30 Hex SHCS -- 18NHX | 60 |  | 4
B18.3.1M - 5 x 0.8 x 20 Hex SHCS -- 20NHX | 61 |  | 7
B18.3.1M - 8 x 1.25 x 40 Hex SHCS -- 28NHX | 62 |  | 8
X Motor Module Motor Holder | 63 |  | 1
X Motor Module Gear | 64 |  | 1
EndStop Spacer 90mm | 65 |  | 2
B18.3.1M - 5 x 0.8 x 12 Hex SHCS -- 12NHX | 66 |  | 2
Z Axis Profile | 67 |  | 1
HGR25-R750 | 68 |  | 2
Butée Supérieure Axe Z | 69 |  | 1
Butée Axe Z | 70 |  | 1
Pose Vis à bille | 71 |  | 1
Z Axis Motor Module Bot | 72 |  | 1
Z Axis Motor Module Top | 73 |  | 1
Z Axis Pulley 17XL037 | 74 |  | 1
Bearing 6001 | 75 |  | 1
DIN 6912 - M8 x 20 --- 13N | 76 |  | 1
B18.3.1M - 5 x 0.8 x 10 Hex SHCS -- 10NHX | 77 |  | 5
B18.3.1M - 4 x 0.7 x 16 Hex SHCS -- 16NHX | 78 |  | 1
900mm | 79 |  | 1
DIN 6912 - M4 x 12 --- 8.5N | 80 |  | 1
16100 | 81 |  | 3
Z2C | 82 |  | 1
DIN 6912 - M6 x 10 --- 4.5N | 83 |  | 2
DIN 912 M8 x 12 --- 12N | 84 |  | 1
B18.3.1M - 5 x 0.8 x 25 Hex SHCS -- 25NHX | 85 |  | 4
B Axis Holder | 86 |  | 1
C Axis Holder | 87 |  | 1
Worm | 88 |  | 2
57BYGH001 | 89 | description | 2
C Axis Worm Extension | 90 |  | 1
B Axis Worm Wheel | 91 |  | 1
C Axis Worm Wheel | 92 |  | 1
6004 | 93 |  | 1
16004 | 94 |  | 1
B Axis Spacer | 95 |  | 1
C Axis Spacer | 96 |  | 1
C Axis Bearing Cover | 97 |  | 1
SwivelHead Cover | 98 |  | 1
Rod Inductif Sensor | 99 |  | 2
GX16-4P | 100 |  | 3
DIN 6912 - M5 x 50 --- 16N | 101 |  | 3
Swivel Head Connector Fixing Plate | 102 |  | 1
DIN 7984 - M3 x 6 --- 4.5N | 103 |  | 2
DIN 7984 - M3 x 8 --- 6.5N | 104 |  | 3
1 x Spindle Bearing Housing | 105 |  | 1
Bearing Spacer | 106 |  | 1
1 x Shank Collet Chuck | 107 |  | 1
Brushless Motor | 108 |  | 1
Top Spacer | 109 |  | 1
Ball Bearing 607 | 110 |  | 2
1 x Housing Spacer | 111 |  | 1
Ball Nose End Mill | 112 |  | 1
B Axis | 113 |  | 1
Spindle Housing | 114 |  | 1
DIN 7984 - M4 x 6 --- 3.9N | 115 |  | 4
DIN 7984 - M3 x 10 --- 8.5N | 116 |  | 1
B18.3.1M - 3 x 0.5 x 40 Hex SHCS -- 18NHX | 117 |  | 4
B18.3.1M - 6 x 1.0 x 10 Hex SHCS -- 10NHX | 118 |  | 1
Plexi Door | 119 |  | 2
Pomelle PVC | 120 |  | 2
B18.3.1M - 8 x 1.25 x 20 Hex SHCS -- 20NHX | 121 |  | 12

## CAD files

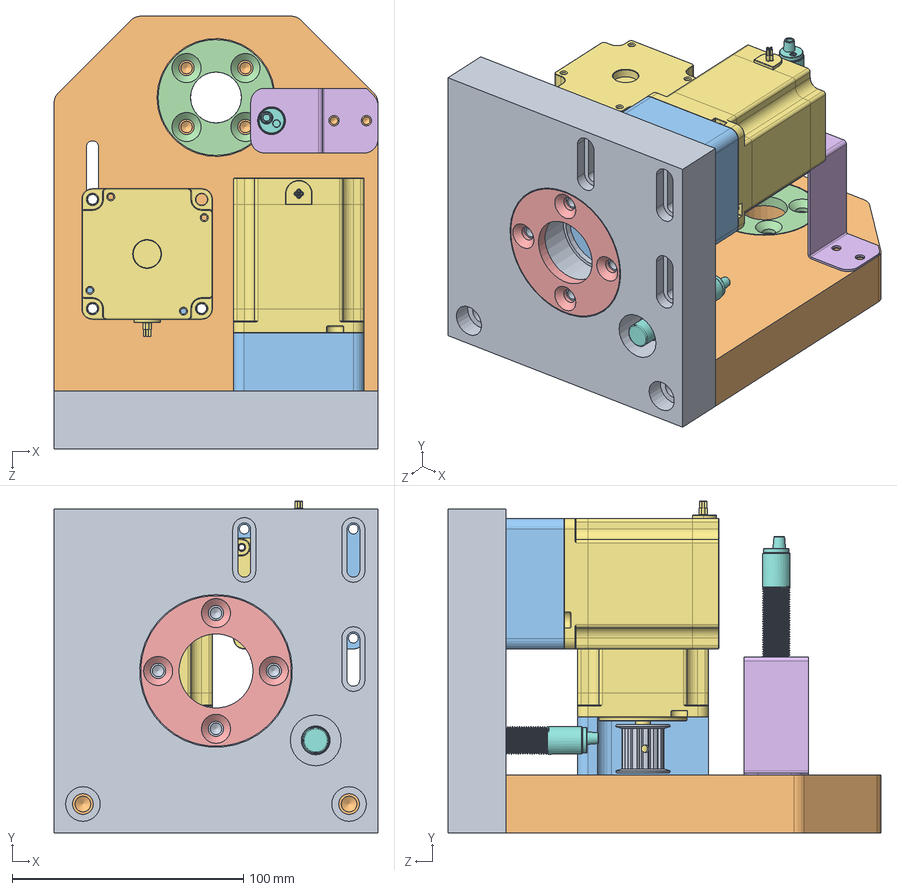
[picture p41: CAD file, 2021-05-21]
CAD/CARVER_X5 v1.1/5 - C Axis/C Axis.SLDASM
140.0 x 143.4 x 187.0 mm
Top v-2
Right Main v-2
Nema 23 Mount C Axis v-2 x 2
Couvercle B Axis
couvercle Roullement C axis v-2
Tole Pliée
NEMA23 Stepper Motor x 2
Rod Inductif Sensor x 2
pulley_p27t5122fa x 2

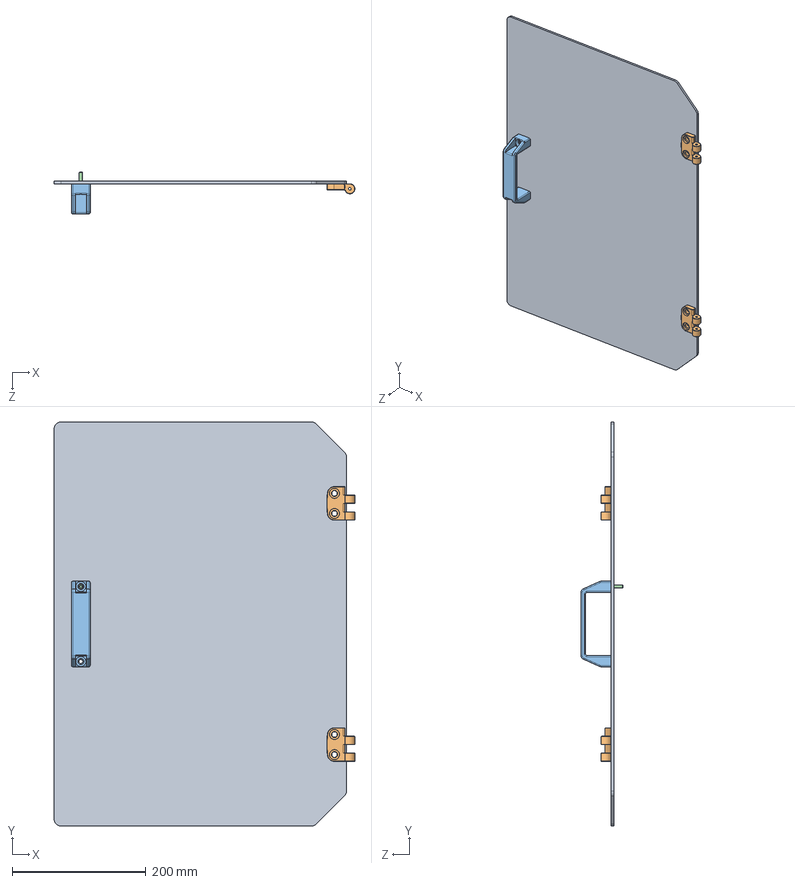
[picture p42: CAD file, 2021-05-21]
CAD/CARVER_X5 v1.1/Machine Doors/Door with Hinges.SLDASM
449.0 x 603.0 x 62.6 mm
Plexi Door
Charnière Polyamide x 2
Pomelle PVC
socket head cap screw_am

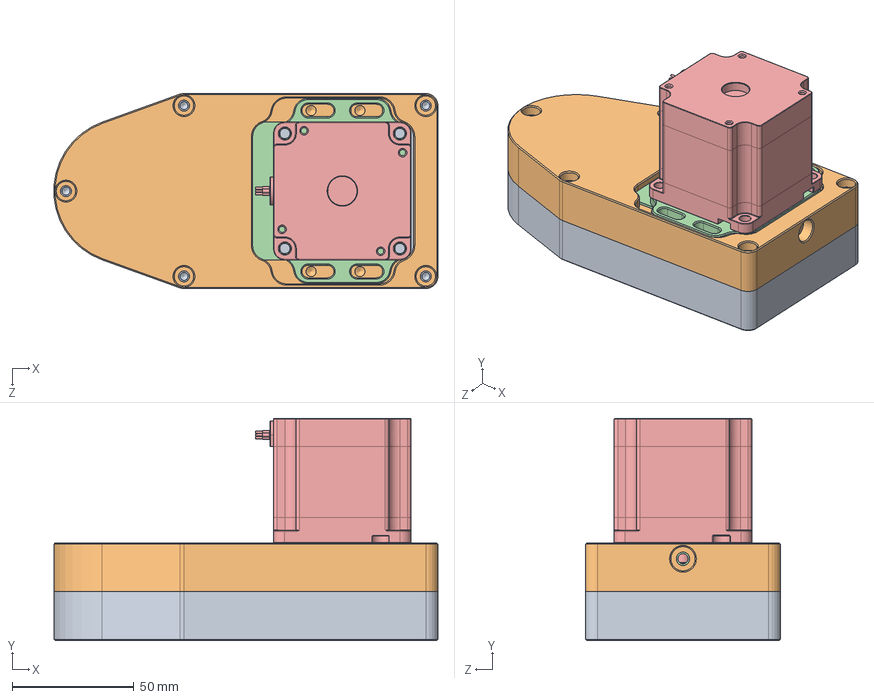
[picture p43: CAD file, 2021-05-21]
CAD/CARVER_X5 v1.1/Motor Modules/Z Motor Module/Z Axis Motor Module.SLDASM
157.4 x 91.0 x 80.0 mm
Z Axis Motor Module Bot
Z Axis Motor Module Top
Z Axis Pulley 17XL037
Tendeur Moteur
NEMA23 Stepper Motor
Motor Pulley 17XL037 6.35mm Bore
Bearing 6001
Wedge 3x3x14
Motor Module Washer

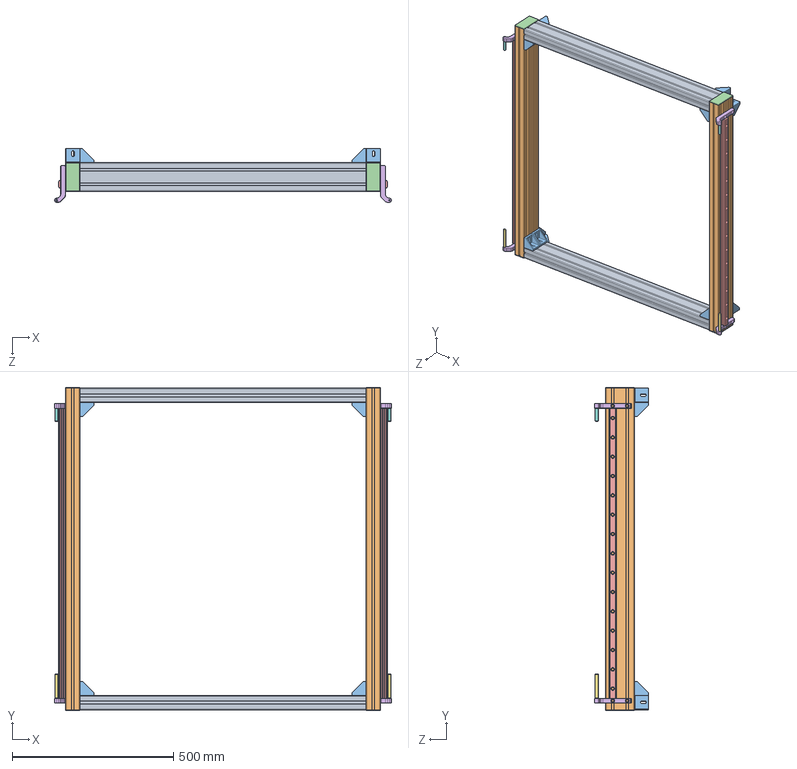
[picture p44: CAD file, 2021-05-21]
CAD/CARVER_X5 v1.1/1 - Base/Frame Top Stage.SLDASM
1046.0 x 1003.0 x 166.5 mm
Frame X Top x 2
Frame Y Top x 2
nervure x 16
Alu Profile End Cap 45x90 x 4
HGR25-R1000 x 2
Y Axis Stop x 4
EndStop Spacer 75mm x 2
EndStop Spacer 40mm x 2

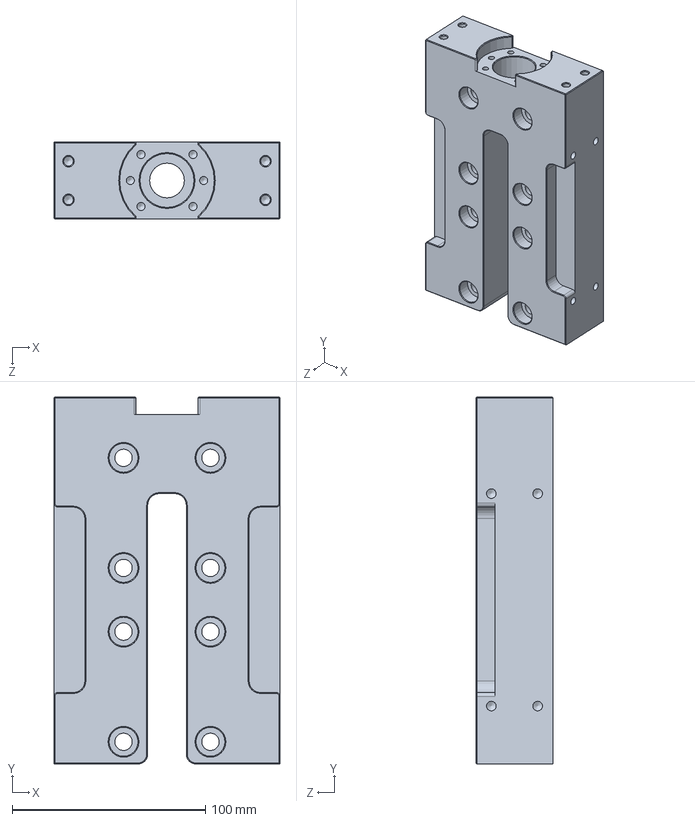
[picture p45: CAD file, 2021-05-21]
CAD/CARVER_X5 v1.1/3 - X Axis/X2Z Main.SLDPRT
117.0 x 190.0 x 40.0 mm

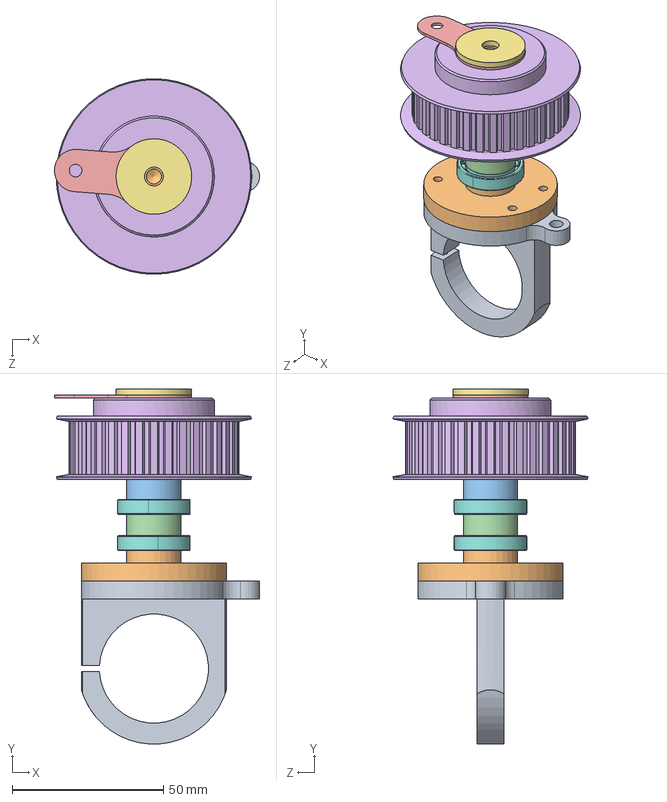
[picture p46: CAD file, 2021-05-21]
CAD/CARVER_X5 v1.1/6 - B Axis/B Axis.SLDASM
67.9 x 117.5 x 64.7 mm
Spindle Housing v2
B Axis
Bague B Axis_4.5mm v-2
Bague Entretoise B axis bearing
Cale Axe B
pulley B Axis
Rondelle B axis v-2

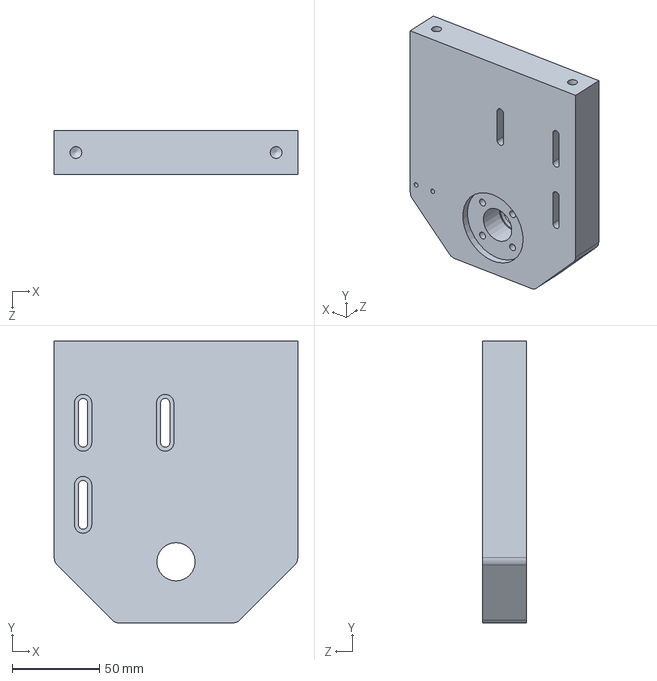
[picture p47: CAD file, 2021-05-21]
CAD/CARVER_X5 v1.1/5 - C Axis/Right Main v-2.SLDPRT
140.0 x 162.0 x 25.0 mm

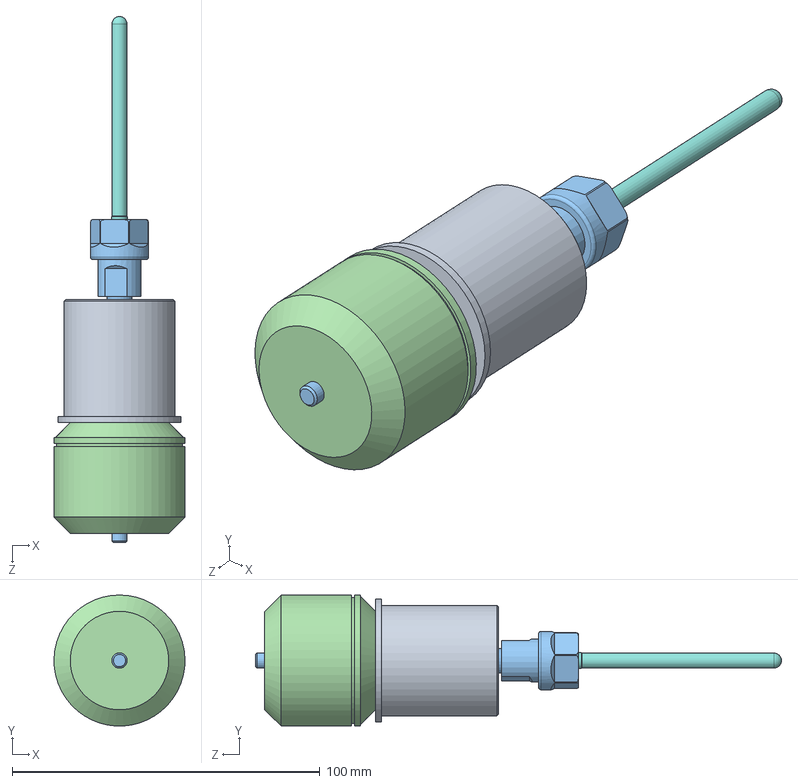
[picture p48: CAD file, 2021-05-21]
CAD/CARVER_X5 v1.1/7 - Spindle Motor/Spindle Motor.SLDASM
42.6 x 42.6 x 171.0 mm
Spindle Bearing Housing
Bearing Spacer
Shank Collet Chuck
Brushless Motor
Top Spacer
Ball Bearing 607 x 2
Housing Spacer
Ball Nose End Mill

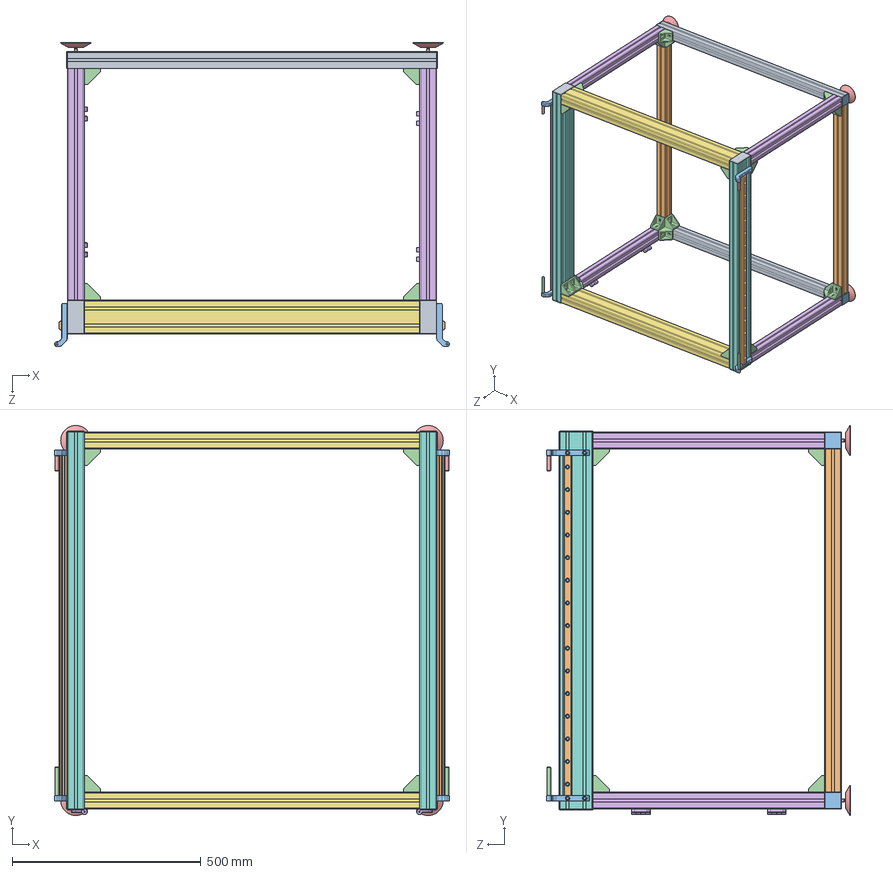
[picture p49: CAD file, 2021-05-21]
CAD/CARVER_X5 v1.1/1 - Base/Base.SLDASM
1046.0 x 1033.0 x 805.5 mm
Frame X Bot x 2
Frame Y Bot x 2
Alu Profile End Cap 45x45 x 4
nervure x 28
Articulated Foot x 4
Frame Z x 4
Frame X Top x 2
Frame Y Top x 2
Alu Profile End Cap 45x90 x 4
HGR25-R1000 x 2
Y Axis Stop x 4
EndStop Spacer 75mm x 2
EndStop Spacer 40mm x 2
Charnière Polyamide x 4

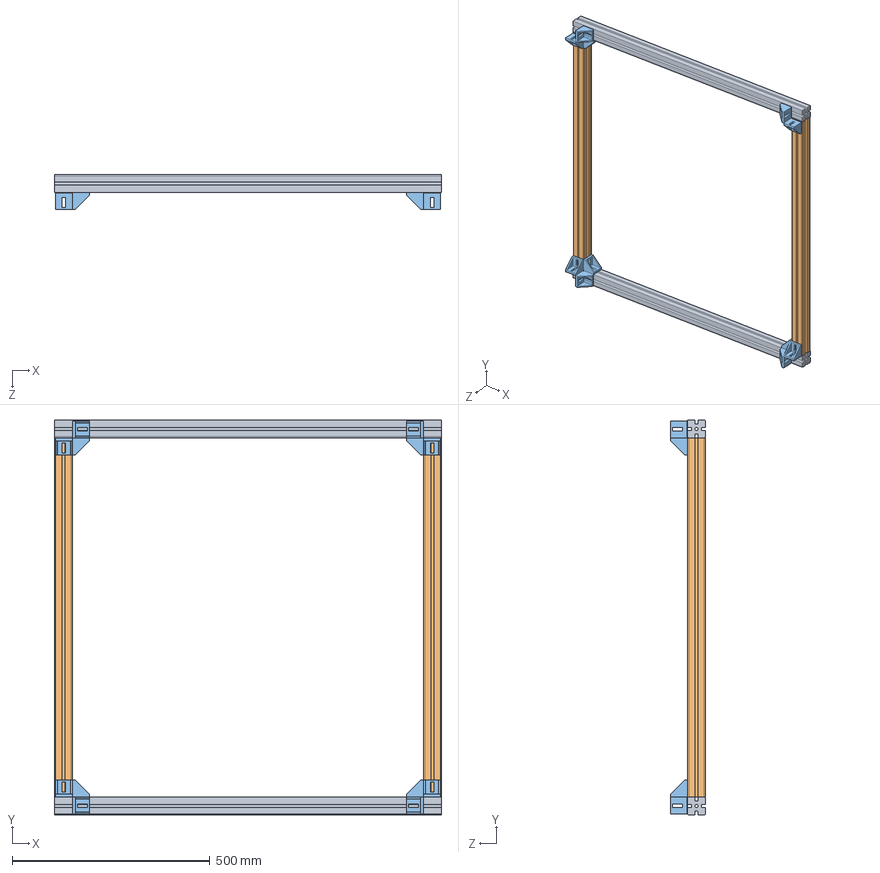
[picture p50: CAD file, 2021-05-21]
CAD/CARVER_X5 v1.1/1 - Base/Frame Bot Stage.SLDASM
978.0 x 998.0 x 88.0 mm
Frame X Bot x 2
Frame Y Bot x 2
nervure x 12

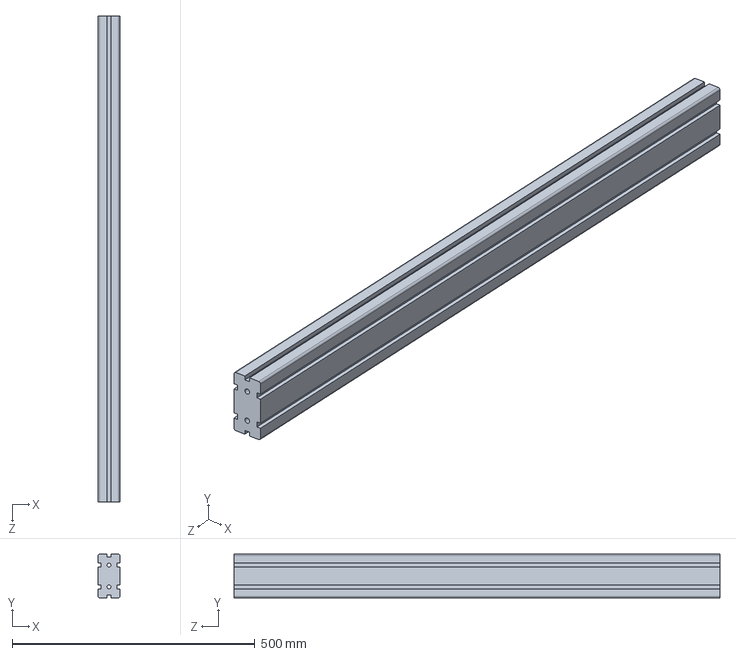
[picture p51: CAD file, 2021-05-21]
CAD/CARVER_X5 v1.1/1 - Base/Frame Y Top.SLDPRT
45.0 x 90.0 x 1000.0 mm

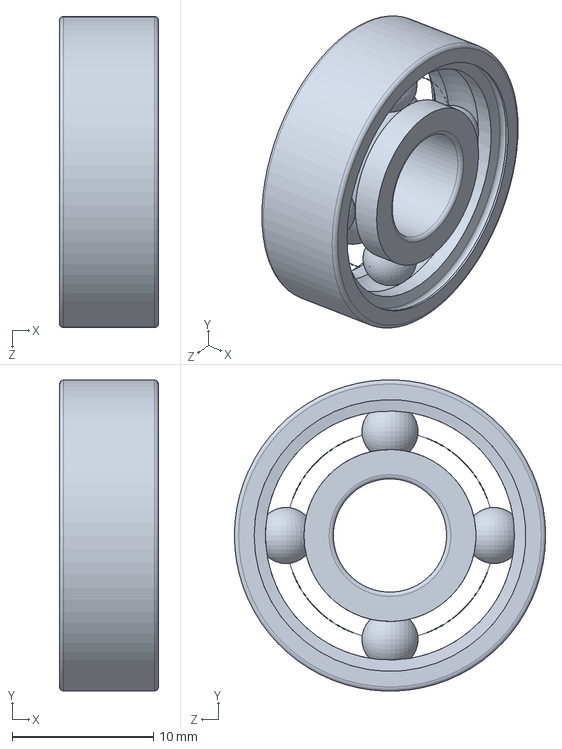
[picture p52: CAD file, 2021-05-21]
CAD/CARVER_X5 v1.1/2 - Y Axis/Bearing 608.SLDPRT
7.00 x 22.0 x 22.0 mm

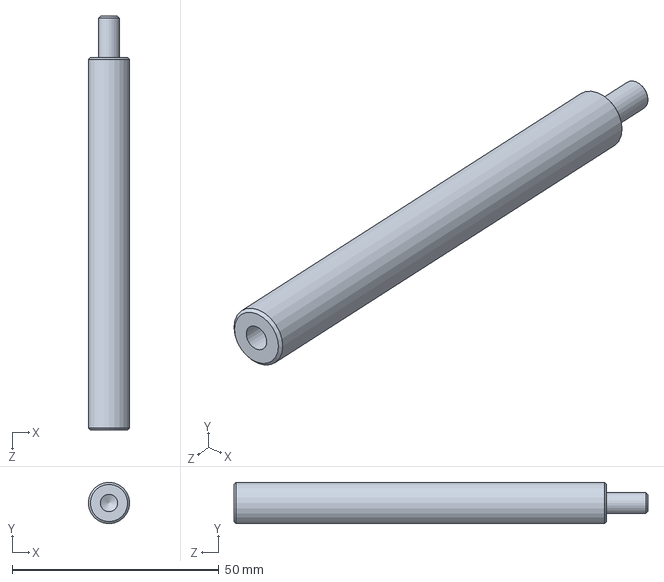
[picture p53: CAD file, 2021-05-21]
CAD/CARVER_X5 v1.1/3 - X Axis/EndStop Spacer 90mm.SLDPRT
10.0 x 10.0 x 100.0 mm

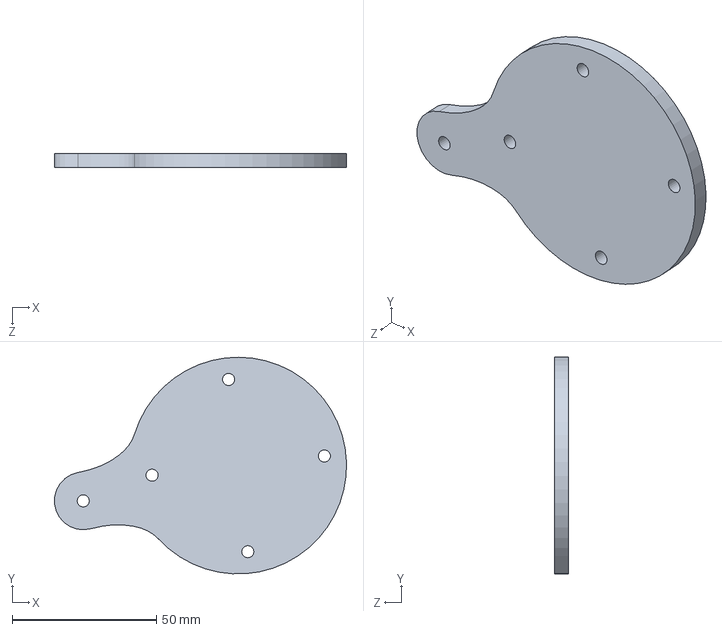
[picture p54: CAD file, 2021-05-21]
CAD/CARVER_X5 v1.1/4 - Z Axis/cale c axis v-2.SLDPRT
101.1 x 74.9 x 5.00 mm

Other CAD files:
CAD/CARVER_X5 v1.1/6 - B Axis/Couvercle B Axis.SLDPRT
CAD/CARVER_X5 v1.1/7 - Spindle Motor/Bearing Spacer.SLDPRT
CAD/CARVER_X5 v1.1/Belt Module/Nema23_Support.SLDPRT
CAD/CARVER_X5 v1.1/Motor Modules/X Motor Module/X Motor Module Motor Holder.SLDPRT
CAD/CARVER_X5 v1.0/1 - Frame - Y Axis/Alu Profile End Cap 45x45.SLDPRT
CAD/CARVER_X5 v1.0/1 - Frame - Y Axis/Alu Profile End Cap 45x90.SLDPRT
CAD/CARVER_X5 v1.0/1 - Frame - Y Axis/Articulated Foot.SLDPRT
CAD/CARVER_X5 v1.0/1 - Frame - Y Axis/EndStop Spacer 40mm.SLDPRT
CAD/CARVER_X5 v1.0/1 - Frame - Y Axis/EndStop Spacer 75mm.SLDPRT
CAD/CARVER_X5 v1.0/1 - Frame - Y Axis/Frame - Y Axis.SLDASM
CAD/CARVER_X5 v1.0/1 - Frame - Y Axis/Frame Bot Stage.SLDASM
CAD/CARVER_X5 v1.0/1 - Frame - Y Axis/Frame Top Stage.SLDASM
CAD/CARVER_X5 v1.0/1 - Frame - Y Axis/Frame X Bot.SLDPRT
CAD/CARVER_X5 v1.0/1 - Frame - Y Axis/Frame X Top.SLDPRT
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

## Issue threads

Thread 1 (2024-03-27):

Question: Nema 23 stepper motor

StephenBrough, 2024-03-27:
Which nema 23 stepper motor was used for this project?

StephenBrough, 2024-05-10:
I think I found it. Looks like it's labled 57BYGH201 on the bill of materials.

Closed 2024-05-10.

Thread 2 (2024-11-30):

v1.1 Y-Axis Belt Assembly

StephenBrough, 2024-11-30:
I'm looking at the SolidWorks file for v1.1 and I don't see how the Y-axis connects to the motor. Looks like a belt is used, but I don't see how it can drive the Y-axis. Does the belt just wrap around the bearings?

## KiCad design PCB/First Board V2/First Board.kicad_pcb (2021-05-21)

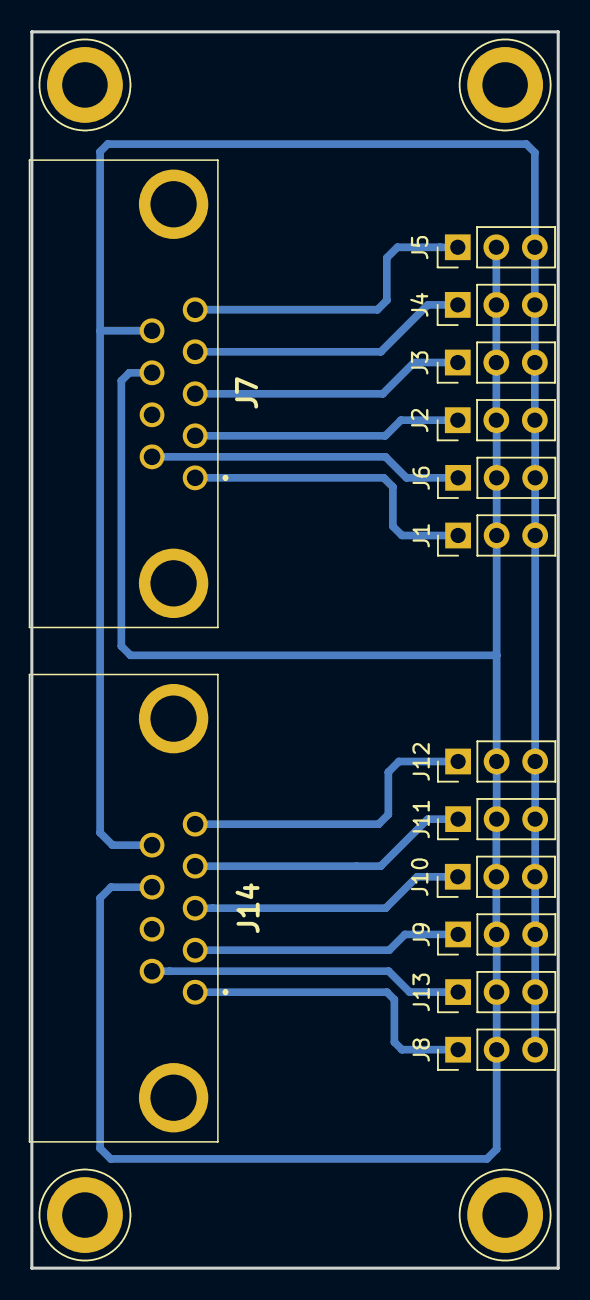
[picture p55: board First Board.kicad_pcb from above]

Board: 2 copper layers, 34.7 x 81.5 mm, 14 parts (0 on the bottom side), 14 nets.

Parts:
J1, J2, J3, J4, J5, J6, J8, J9, J10, J11, J12, J13: Conn_01x03_Male; PinHeader_1x03_P2.54mm_Vertical
J7, J14: DB9_Female; 182009213R531

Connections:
+12V: J1.2, J2.2, J3.2, J4.2, J5.2, J6.2, J7.8, J8.2, J9.2, J10.2, J11.2, J12.2, J13.2, J14.8
GND: J1.3, J2.3, J3.3, J4.3, J5.3, J6.3, J7.9, J8.3, J9.3, J10.3, J11.3, J12.3, J13.3, J14.9
unnamed: J1.1, J7.1
unnamed: J2.1, J7.2
unnamed: J3.1, J7.3
unnamed: J4.1, J7.4
unnamed: J5.1, J7.5
unnamed: J6.1, J7.6
unnamed: J10.1, J14.3
unnamed: J11.1, J14.4
unnamed: J12.1, J14.5
unnamed: J13.1, J14.6
unnamed: J8.1, J14.1
unnamed: J9.1, J14.2

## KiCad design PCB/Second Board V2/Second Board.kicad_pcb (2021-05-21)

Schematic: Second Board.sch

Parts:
D1, D2, D3, D4, D5, D6, D7, D8, D9, D10, D11, D12: LED_ALT; LED_D3.0mm
J1, J2, J4: 691322110008; SHDR8W120P0X508_1X8_4264X1200X860P; Manufacturer_Part_Number 691322110008; Mouser Part Number 710-691322110008
J3: Conn_01x02_Female; TerminalBlock_bornier-2_P5.08mm
J5: Conn_02x10_Odd_Even; PinHeader_2x10_P2.54mm_Vertical
R1, R2, R3, R4, R5, R6, R7, R8, R9, R10, R11, R12: 10K; R_Axial_DIN0207_L6.3mm_D2.5mm_P7.62mm_Horizontal
U1, U2, U3, U4, U5, U6, U7, U8, U9, U10, U11, U12: LTV-817; DIP-4_W7.62mm

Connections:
+12V: J1.2, J3.2, J4.2
CMD1: J2.1, U1.4
CMD2: J2.2, U2.4
CMD3: J2.3, U3.4
CMD4: J2.4, U4.4
CMD5: J2.5, U5.4
CMD6: J2.6, U6.4
CMD7: J5.7, U7.4
CMD8: J5.9, U8.4
CMD9: J5.11, U9.4
CMD10: J5.13, U10.4
CMD11: J5.15, U11.4
CMD12: J5.17, U12.4
GND: D1.1, D2.1, D3.1, D4.1, D5.1, D6.1, D7.1, D8.1, D9.1, D10.1, D11.1, D12.1, J1.1, J3.1, J4.1
GNDPWR: J2.8, J5.1, J5.19, U1.3, U2.3, U3.3, U4.3, U5.3, U6.3, U7.3, U8.3, U9.3, U10.3, U11.3, U12.3
unnamed: D1.2, R1.2
unnamed: D2.2, R2.2
unnamed: D3.2, R3.2
unnamed: D4.2, R4.2
unnamed: D5.2, R5.2
unnamed: D6.2, R6.2
unnamed: D7.2, R7.2
unnamed: D8.2, R8.2
unnamed: D9.2, R9.2
unnamed: D10.2, R10.2
unnamed: D11.2, R11.2
unnamed: D12.2, R12.2
unnamed: R1.1, U1.2
unnamed: R2.1, U2.2
unnamed: R3.1, U3.2
unnamed: R4.1, U4.2
unnamed: R5.1, U5.2
unnamed: R6.1, U6.2
unnamed: R7.1, U7.2
unnamed: R8.1, U8.2
unnamed: R9.1, U9.2
unnamed: R10.1, U10.2
unnamed: R11.1, U11.2
unnamed: R12.1, U12.2
SIG1: J1.8, U1.1
SIG2: J1.7, U2.1
SIG3: J1.6, U3.1
SIG4: J1.5, U4.1
SIG5: J1.4, U5.1
SIG6: J1.3, U6.1
SIG7: J4.8, U7.1
SIG8: J4.7, U8.1
SIG9: J4.6, U9.1
SIG10: J4.5, U10.1
SIG11: J4.4, U11.1
SIG12: J4.3, U12.1

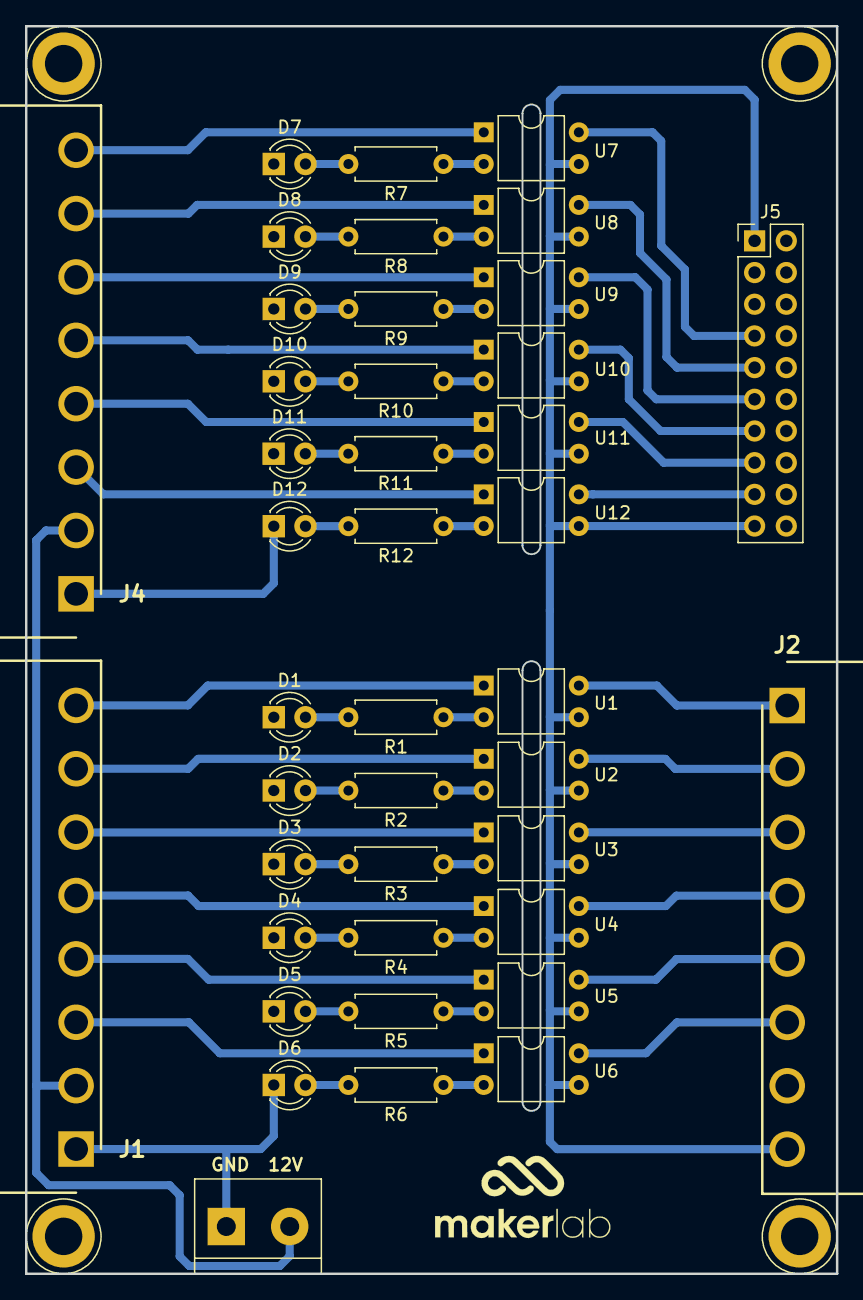
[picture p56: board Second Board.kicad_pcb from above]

Board: 2 copper layers, 65.0 x 100.0 mm, 41 parts (0 on the bottom side), 51 nets.

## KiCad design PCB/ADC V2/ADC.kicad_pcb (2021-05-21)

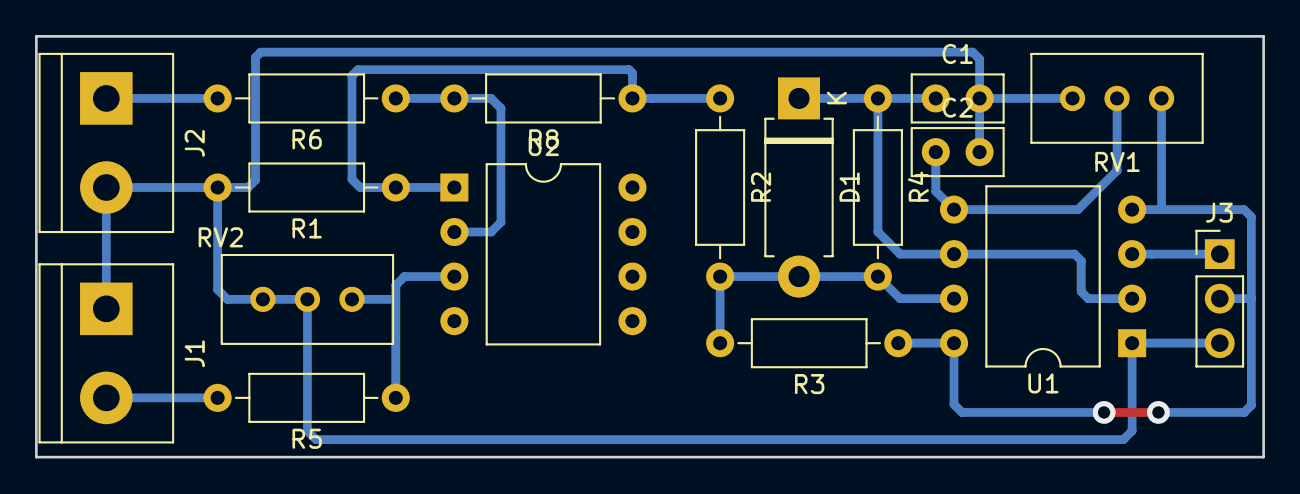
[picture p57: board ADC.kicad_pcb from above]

Board: 2 copper layers, 70.0 x 24.0 mm, 17 parts (0 on the bottom side), 11 nets.

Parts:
C1: 220nF; C_Disc_D5.0mm_W2.5mm_P2.50mm
C2: 100nF; C_Disc_D5.0mm_W2.5mm_P2.50mm
D1: D_ALT; D_DO-15_P10.16mm_Horizontal
J1, J2: Conn_01x02_Female; TerminalBlock_bornier-2_P5.08mm
J3: Conn_01x03_Female; PinHeader_1x03_P2.54mm_Vertical
R1: 47K; R_Axial_DIN0207_L6.3mm_D2.5mm_P10.16mm_Horizontal
R2, R4: 100K; R_Axial_DIN0207_L6.3mm_D2.5mm_P10.16mm_Horizontal
R3: 33R; R_Axial_DIN0207_L6.3mm_D2.5mm_P10.16mm_Horizontal
R5, R6, R8: R; R_Axial_DIN0207_L6.3mm_D2.5mm_P10.16mm_Horizontal
RV1: 470R; Potentiometer_Bourns_3296W_Vertical
RV2: R_POT; Potentiometer_Bourns_3296W_Vertical
U1: TLC555; DIP-8_W10.16mm
U2: LM358; DIP-8_W10.16mm

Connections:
+5V: J3.2, R3.1, RV1.3, U1.4, U1.8
+12V: J1.2, R5.2
ANALOG: J2.1, R6.2
GND: C1.2, C2.2, J1.1, J2.2, J3.3, R1.2, RV1.1, RV2.2, RV2.3, U1.1
unnamed: C1.1, D1.1, R4.1, U1.2, U1.6
unnamed: C2.1, RV1.2, U1.5
unnamed: D1.2, R2.2, R3.2, R4.2, U1.7
unnamed: R1.1, R2.1, R8.1, U2.1
unnamed: R5.1, RV2.1, U2.3
unnamed: R6.1, R8.2, U2.2
PWM: J3.1, U1.3
